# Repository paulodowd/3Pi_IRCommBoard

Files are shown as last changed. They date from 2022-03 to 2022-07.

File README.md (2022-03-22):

# 3Pi_IRCommBoard (work in progress)

<p align="center">
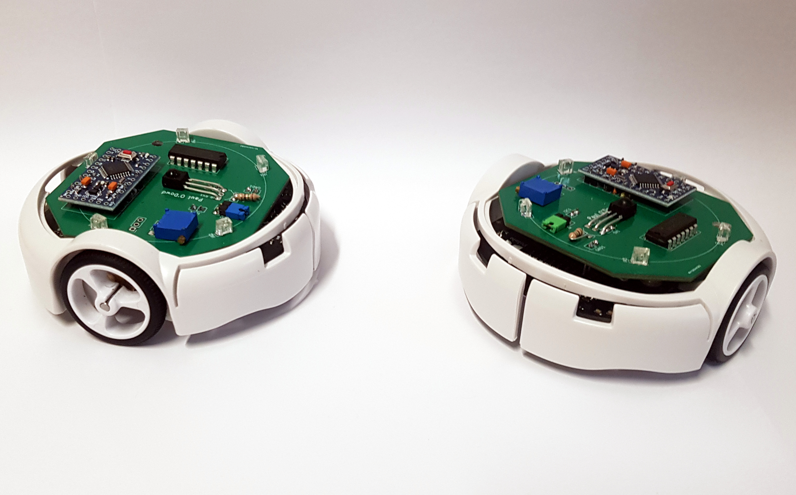
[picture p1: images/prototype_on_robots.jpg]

  </p>

## Features

- Can be considered a general purpose I2C extension board to provide local infra-red (IR) communication.
- IR Serial transmission at 4800 Baud.
- Transmit/receive upto 28 bytes (currently, extensible).
- Range can be reduced/set with a trimmer potentiometer.
- Effective IR transmit range approximately 30cm.
- Message corruption detection implemented with a CRC checksum.
- Designed to conveniently fit to an expansion header of the Pololu 3Pi+ mobile robot. 

## Summary

A pcb design to create infra-red (IR) communication between Pololu 3Pi+ robots. The design utilises an Arduino Pro Mini as an I2C Slave device.  The pro mini handles all transmit and receive operations over IR. The Master device (inteded as the 3Pi+, but could be any device with I2C) can upload a string to transmit, and also request the latest string received, if any.  This can get a little confusing to discuss: I2C is used to transfer messages between Master and Slave, and Serial/IR is used to tranmit messages between Slave devices.  

IR communication is implemented using the standard Serial functionality common to Arduino (e.g. `Serial.print()`), and so the IR circuit is electronically connected to  the Arduino TX and RX pins.  The detection (receiving) circuit uses a Demodulator chip that is tuned for a carrier frequency of 38.4Khz (more details below).  Therefore, the pro mini generates a 38Khz signal via an internal timer interrupt to provide the transmitting carrier, output on digital pin 4.  

The 38Khz carrier signal is combined electronically with the TX pin state through an OR gate (74xx32). The logic (OR) of this operation is defined by the gates sinking the current through the tranmitting IR LEDs.  Therefore, the LEDs are not driven by the 74xx32 (or the pro mini, to be clear), and are considered active low.  A nice unintended side effect of this is that when TX is inactive (LOW, not transmitting), the 74xx32 output is HIGH despite the continued 38Khz signal generation - which means the IR LEDs are off and not saturating the environment.

In this circuit design, a single gate is used to sink current.  It might be important to note that the <a href="https://www.ti.com/lit/ds/symlink/sn54hc32-sp.pdf">datasheet</a> for the logic gates specifies a max current sink of 50ma through ground - and here we are potentially sinking upto 250ma from the 5 IR LEDs.    So far, I've not seen any significant changes to performance and this may be because I am not sinking current continuously, instead intermitently at 38Khz. In a subsequent design (available <a href="https://github.com/paulodowd/Swarm-Bs">here</a>), all 4 gates are ganged, but the internal ground connection may still be a limitation. In either case, I haven't yet seen any problems or difference in performance.  It might be unwise to active the IR LEDs continuously.

Some messages transmitted over IR do get garbled.  As a quick solution, the firmware uses a CRC checksum.  I've used the same implementation as detailed on the RepRap wiki for GCode (<a href="https://reprap.org/wiki/G-code#Checking">here</a>).  Prior to transmitting, the pro mini generates a single byte checksum value, and appends this to the message string.  Therefore, when a message is received, the receiving pro mini completes the same CRC check on the received message for itself, and then compares if the checksum values match.  If not, some data must be corrupt and the message is discarded.  

The message strings transmitted between the pro mini devices would look something like:

`*message string@f`

Here, the `*` is used to identify the start of a message, the `@` is used to identify the end of the message and that the next byte is the checksum value.  In the example above, I haven't used the correct checksum value, it is just an illustrative example.  The transmission is also made with a `\n` character at the end, but this is discarded.  

At the moment, the pro mini firmware will only store 1 message, the latest message received.  Furthermore, it is programmed to erase this message after 1 second.  This suits the intended use of the board, but will likely need updating for other uses.  

When the Master device requests the latest message from the pro mini Slave device, it will receive a string terminated with a `!` character.  If the Master receives:

`!` 

This means that no messages are available.  Otherwise, the Master can parse the received bytes over I2C and use the `!` to identify the end of the string (more details below).  

If the Master is to set a string for the pro mini Slave to transmit over IR, this should be sent over I2C with no terminating character (e.g., no newline, or anything specific, just the string you wish to transmit).  Here, it is unknown (not tested!) what will happen if your string has an `*`, `\n` or `!` in it - it will probably break functionality!  Whilst this is inconsistent from the format used for messages between the pro mini Slave devices, it presents the simplest usage/interface when working with the Master device - all the tokens and CRC are handled for the user.

Software is still sketchy early work for proof-of-concept.

## Important Considerations

- **IR Demodulator:** I tried a few IR demodulator chips and they are not all created equally.  In particular, those designed to receive bursts of transmission appear poorly suited.  When using ones for burst transmission, I observed that I had to wave the transmitter or receiver around to get a successful transmission (perhaps some inner circuitry reaches a saturation?).  Instead it is better to use those designed for continuous transmission. The Vishay **TSDP34138** (<a href="https://www.farnell.com/datasheets/2245004.pdf">datasheet</a>) seems to fit this and works well / reliably.  The datasheet specifies upto 4800 baud for a 38.4Khz carrier frequency.  If you want to reproduce this board, I recommend you use the same device, or be ready for some trials of different devices.
- **IR Demodulator Placement:** The IR Demodulator (IRD) is placed central on the PCB and facing upwards - this probably isn't the manufacturers recommendation for optimal performance.  I did consider placing 5 IRD's around the circumference of the PCB facing outward between the IR LEDs.  However, the IRD is one of the more expensive components, and so producing 100 of these PCBs would be significantly more expensive with 5 IRD per board.  I have tested this PCB with 1 upward IRD and it can reliably detect IR transmission from neighbours at roughly 30cm distance.  For communication between Pololu 3Pi+ robots, this is relatively "local" and sufficient.  However, it does mean a robot cannot identify from which direction a transmission was received.  In theory, I think a more advanced version of this board could supply VCC to 5 independent IRD via the arduino digital pins, and therefore poll the IRD around the circumference of the board by enabling each in turn, and so infer directionality.  But I haven't tried this. 
- **Self-Receiving:** I did have an issue of a single board receiving it's own IR transmissions, and not being able to receive transmission from neighbours.  I believe this is because the UART implementation (on the Atmega328 at least) operates send (TX) and receive (RX) independently.  When using IR light, this means it will detect it's own transmission. After attempting a lot of different solutions, it was as simple as disabling the RX functionality of the UART by a register operation.  I'm glad this was available!  You can review the details of this on page 171 of the Atmega328 datasheet (<a href="https://ww1.microchip.com/downloads/en/DeviceDoc/Atmel-7810-Automotive-Microcontrollers-ATmega328P_Datasheet.pdf">here</a>).  You can find this operation in the firmware about <a href="https://github.com/paulodowd/3Pi_IRCommBoard/blob/922e04242b78fc39a44c0d518355c1a5028df249/arduino/pro_mini_firmware/pro_mini_firmware.ino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">here</a>.
- **Programming the Pro Mini:** It is important to note that the programming of the Pro Mini will most often fail if the IR Demodulator is electronically connected.  Therefore, the circuit design has a jumper (labelled, "RX Break") intended for a connecting removable sleeve, to allow the connection to be broken for programming.  Importantly, no IR messages can be received if this jumper is not closed with the sleeve.  
- **I2C requests from Master:** so far, it seems that the Master device has to request a specific number of bytes from the Slave device.  Because we don't necessarily know this before hand (and to take a short cut), the firmware has been written to append a `!` character to the end of the message string.  Therefore, the Master requests the maximum data length, and then parses for the `!` character.  After this, the data is gibberish.  In the future, it might be better to have a two step operation where the Master first asks how large the data to transfer is.  
- **Buffer Sizes:** The current buffers for sending and receiving IR messages in the firmware are set to 32 bytes (`MAX_MSG = 32`).  The IR transmission is operated by the Arduino Serial functionality.  By default, the Arduino environment sets the Serial buffer to 64 bytes.  Here, I decided to keep the Serial buffer under-utilised (half-full).  My un-tested rationale was to stand a chance of successfully parsing a whole 32-byte message within a 64-byte buffer.  I believe it is possible to expand the default Serial buffer beyond 64 bytes.  These aspects are open for investigation.  But for now, it is recommended to send a string of max length 28 bytes (leaving 4 bytes free for `*`, `@` and the checksum value).  The current buffer implementation for the IR messages is not very clever, e.g. not circular or anything like that.  I haven't validated the reliability of the transmission when the maximum buffer is used. 
- **Buffer Sizes:** The current buffers for sending and receiving IR messages in the firmware are set to 32 bytes (`MAX_MSG = 32`).  The IR transmission is operated by the Arduino Serial functionality.  By default, the Arduino environment sets the Serial buffer to 64 bytes.  Here, I decided to keep the Serial buffer under-utilised (half-full).  My un-tested rationale was to stand a chance of successfully parsing a whole 32-byte message within a 64-byte buffer.  I believe it is possible to expand the default Serial buffer beyond 64 bytes.  These aspects are open for investigation.  But for now, it is recommended to send a string of max length 28 bytes (leaving 3 bytes free for `*`, `@`, the checksum value and `\n`).  The current buffer implementation for the IR messages is not very clever, e.g. not circular or anything like that.  I haven't validated the reliability of the transmission when the maximum buffer is used. 
- **IR Message Buffers:** to buffer messages being sent and received, there are 3 buffers in total. 1) a buffer to hold the message to transmit as set by the Master 2) a buffer to process a received message 3) a buffer to hold the last correctly validated message to relay to the Master.  Therefore, buffer 2 could be considered volatile - hence the need for 3 buffers.  
- **IR LED current:**  In this circuit design, a single gate is used to sink current.  It might be important to note that the <a href="https://www.ti.com/lit/ds/symlink/sn54hc32-sp.pdf">datasheet</a> for the logic gates specifies a max current sink of 50ma through ground - and here we are potentially sinking upto 250ma from 5 IR LEDs.    So far, I've not seen any significant changes to performance and this may be because I am not sinking current continuously. In a subsequent design (available <a href="https://github.com/paulodowd/Swarm-Bs">here</a>), all 4 gates are ganged, but the internal ground connection may still be a limitation. In either case, I haven't yet seen any problems or difference in performance.  It might be unwise to active the IR LEDs continuously.

## Bill of Materials (BOM)

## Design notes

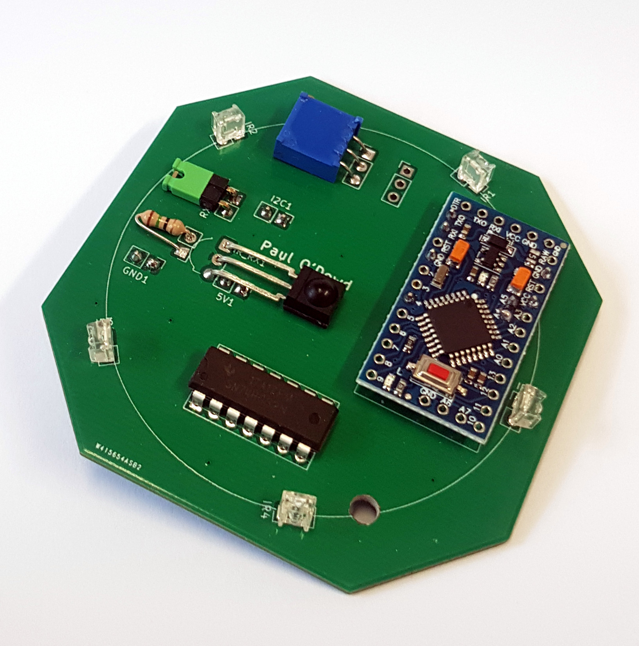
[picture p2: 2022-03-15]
images/board_prototype.jpg

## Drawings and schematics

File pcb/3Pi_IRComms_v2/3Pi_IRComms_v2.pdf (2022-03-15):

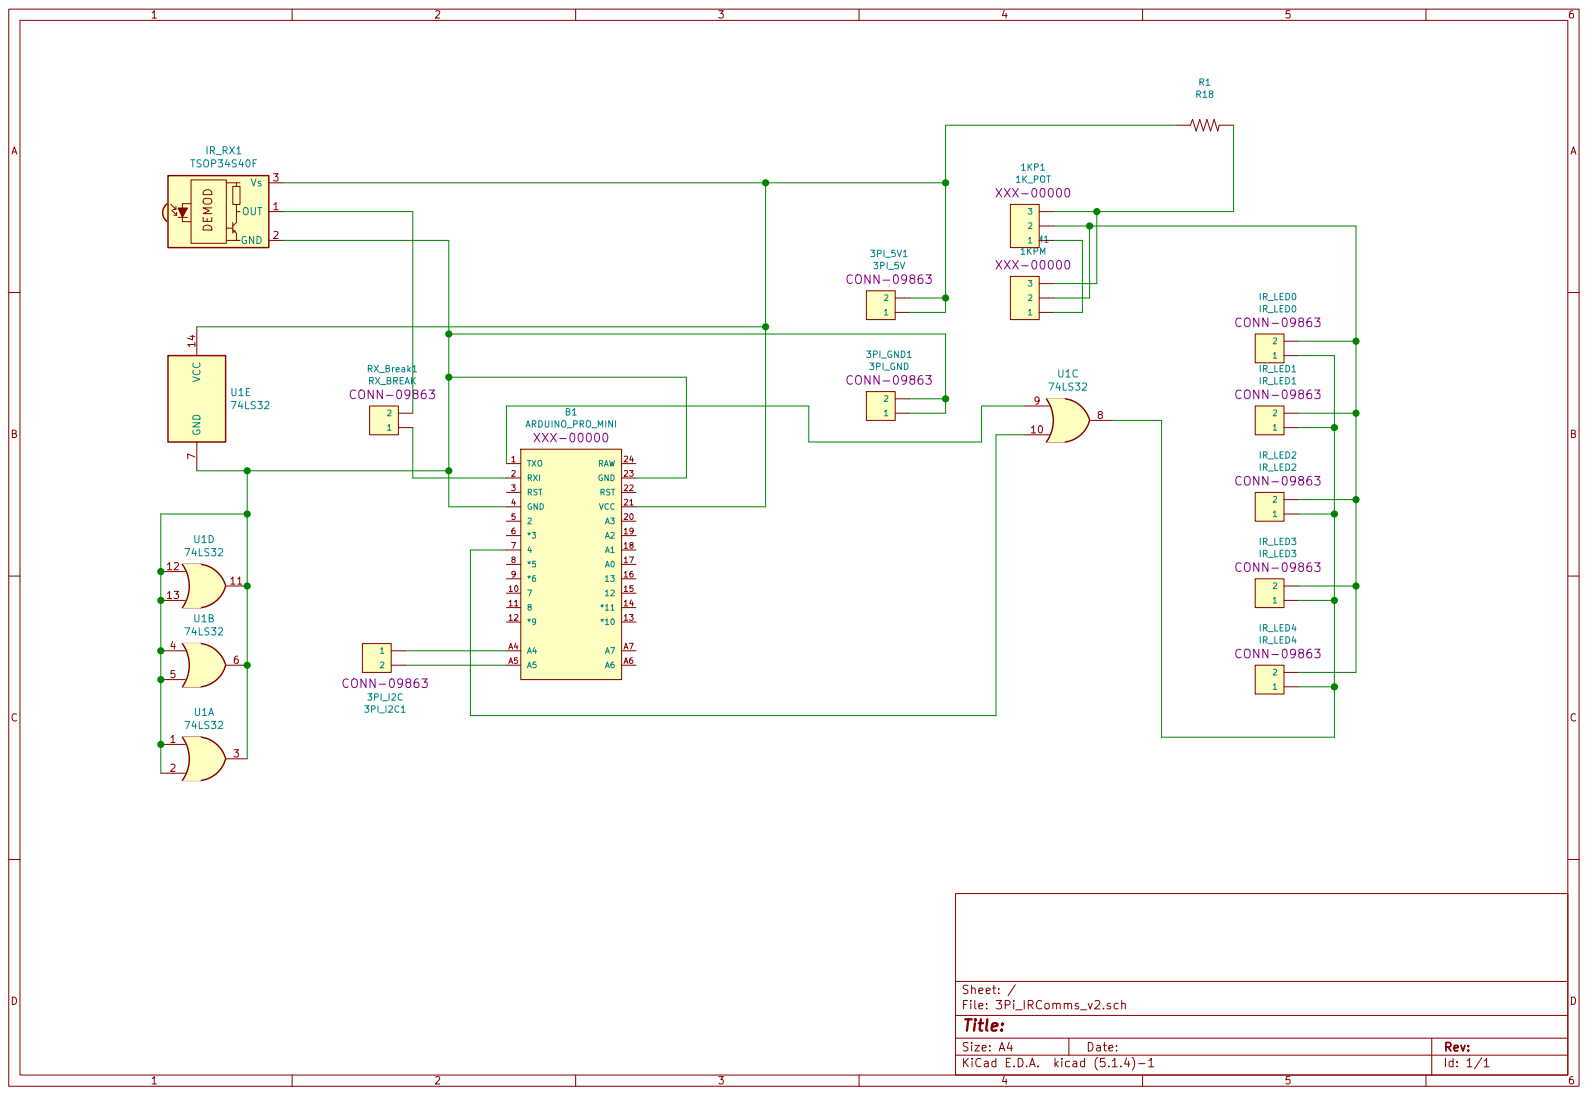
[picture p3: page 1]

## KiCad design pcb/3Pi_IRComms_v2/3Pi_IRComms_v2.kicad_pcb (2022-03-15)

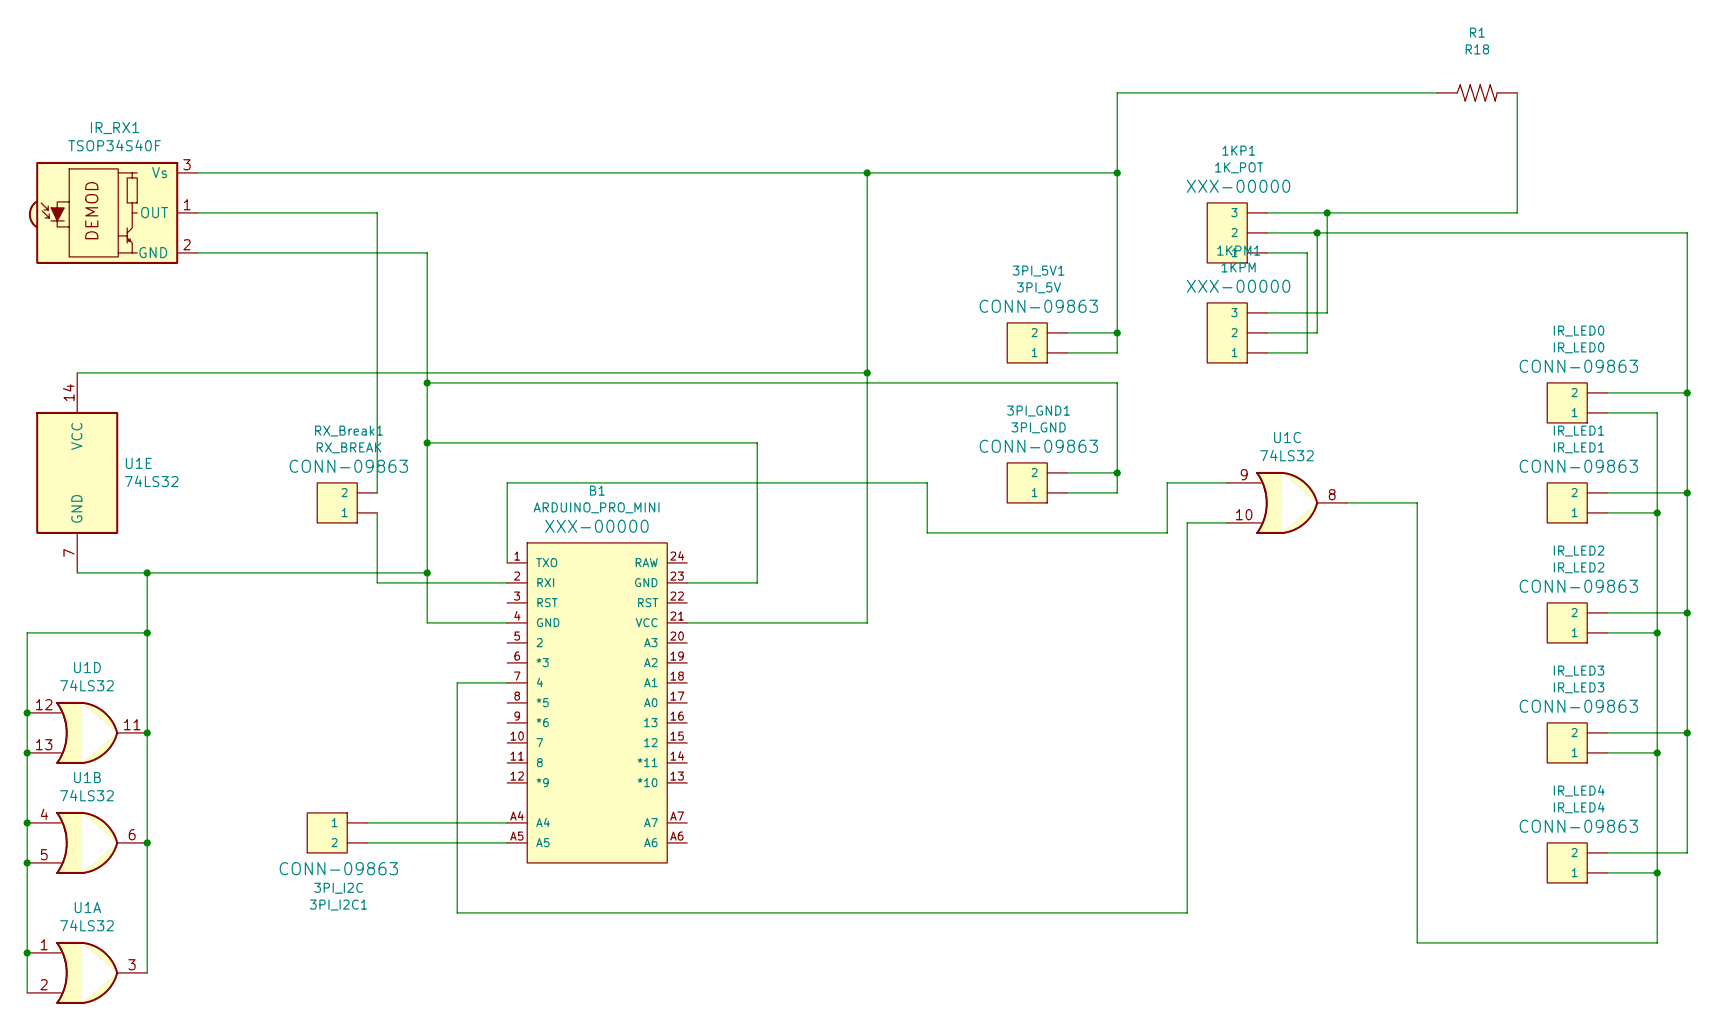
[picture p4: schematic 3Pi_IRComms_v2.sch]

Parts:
1KP1: 1K_POT; PinHeader_1x03_P2.54mm_Vertical
1KPM1: 1KPM; PinHeader_1x03_P2.54mm_Vertical
3PI_5V1: 3PI_5V; PinHeader_1x02_P2.54mm_Vertical
3PI_GND1: 3PI_GND; PinHeader_1x02_P2.54mm_Vertical
3PI_I2C1: 3PI_I2C; PinHeader_1x02_P2.54mm_Vertical
B1: ARDUINO_PRO_MINI
IR_LED0: IR_LED0; PinHeader_1x02_P2.54mm_Vertical
IR_LED1: IR_LED1; PinHeader_1x02_P2.54mm_Vertical
IR_LED2: IR_LED2; PinHeader_1x02_P2.54mm_Vertical
IR_LED3: IR_LED3; PinHeader_1x02_P2.54mm_Vertical
IR_LED4: IR_LED4; PinHeader_1x02_P2.54mm_Vertical
IR_RX1: TSOP34S40F; Vishay_MOLD-3Pin
R1: R18; PinHeader_1x02_P2.54mm_Vertical
RX_Break1: RX_BREAK; PinHeader_1x02_P2.54mm_Vertical
U1: 74LS32; DIP-14_W7.62mm_Socket

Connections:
unnamed: 1KP1.1, 1KPM1.1
unnamed: 1KP1.2, 1KPM1.2, IR_LED0.2, IR_LED1.2, IR_LED2.2, IR_LED3.2, IR_LED4.2
unnamed: 1KP1.3, 1KPM1.3, R1.2
unnamed: 3PI_5V1.1, 3PI_5V1.2, B1.21 (VCC), IR_RX1.3 (Vs), R1.1, U1.14 (VCC)
unnamed: 3PI_GND1.1, 3PI_GND1.2, B1.4 (GND), B1.23 (GND), IR_RX1.2 (GND), U1.1, U1.2, U1.3, U1.4, U1.5, U1.6, U1.7 (GND), U1.11, U1.12, U1.13
unnamed: 3PI_I2C1.1, B1.A4
unnamed: 3PI_I2C1.2, B1.A5
unnamed: B1.1 (TXO), U1.9
unnamed: B1.2 (RXI), RX_Break1.1
unnamed: B1.7 (4), U1.10
unnamed: IR_LED0.1, IR_LED1.1, IR_LED2.1, IR_LED3.1, IR_LED4.1, U1.8
unnamed: IR_RX1.1 (OUT), RX_Break1.2

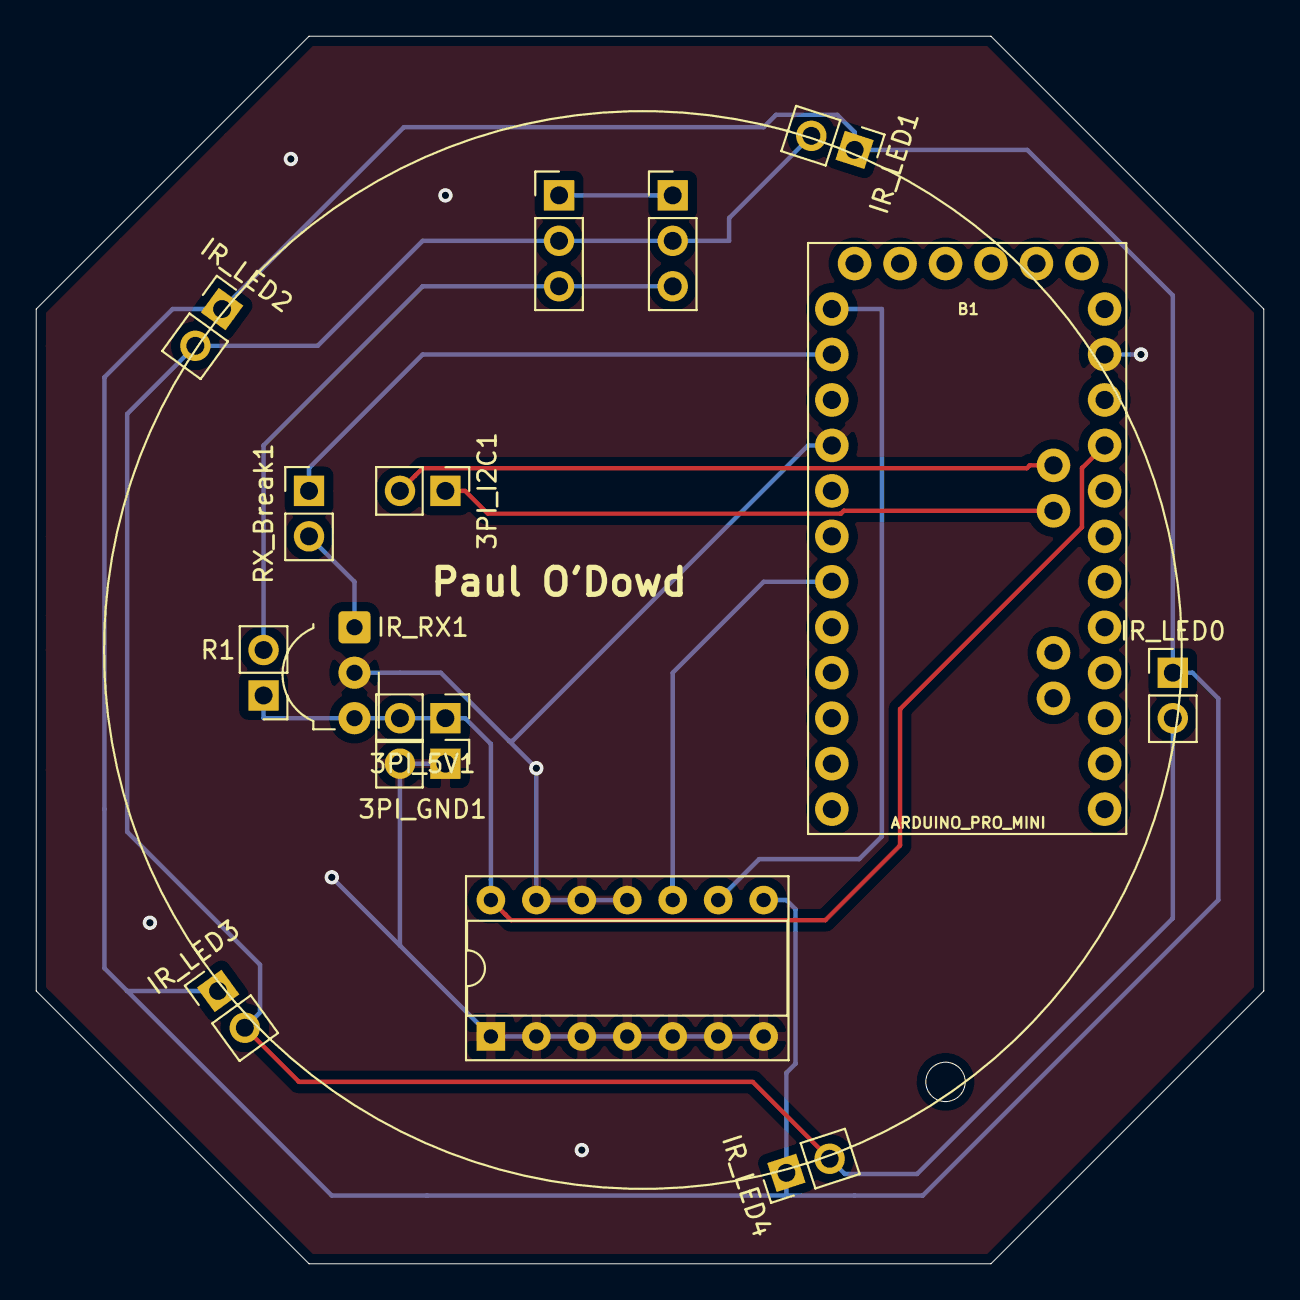
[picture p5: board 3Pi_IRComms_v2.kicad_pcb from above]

Board: 2 copper layers, 68.6 x 68.6 mm, 15 parts (0 on the bottom side), 12 nets.

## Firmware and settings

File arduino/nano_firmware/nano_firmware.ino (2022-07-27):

/*
   i2c slave device to handle IR messaging between
   3pi+ robots.
*/
#include <avr/io.h>
#include <Wire.h>
#define I2C_ADDR 8

boolean LED;      // debug LED
unsigned long ts; // general time stamp, timeout for
                  // debug LED.

#define POT_A A0
#define POT_B A1
#define POT_C A2

// Two operational states
#define STATE_IR_TX_ON 1
#define STATE_IR_TX_OFF 2
int state = STATE_IR_TX_ON;


#define MAX_MSG 32
static char tx_buf[MAX_MSG];  // buffer for IR out (serial)
static char rx_buf[MAX_MSG];  // buffer for IR in  (serial)
static char rx_msg[MAX_MSG];  // holding buffer for msg down 
                              // to Master over i2c
int rx_count;

// 38Khz signal generated on
// digital pin 4.
#define TX_CLK_OUT 4

unsigned long msg_ttl; // msg time to live
#define TTL 1000       // keep a message for 1 second
                       // then delete. 

unsigned long tx_ts;    // transmit time-stamp
unsigned long tx_delay; // delay between tx
unsigned long tx_delay_min;
unsigned long tx_delay_extra;

// Flags
boolean BROADCAST = false;
boolean PROCESS_MSG = false;
#define LED_B 9
#define LED_G 10
#define LED_R 11

#define DEBUG_LED 13

void setup() {

  // Set random seed.
  initRandomSeed();

  // Set pin for 38khz carrier as output
  pinMode(TX_CLK_OUT, OUTPUT);

  // Debug led
  pinMode(13, OUTPUT);
  
  // RGB LED
  pinMode( LED_R, OUTPUT );
  pinMode( LED_G, OUTPUT );
  pinMode( LED_B, OUTPUT );

  // Debugging LED
  pinMode(DEBUG_LED, OUTPUT );
  digitalWrite(DEBUG_LED, LOW);

  // Input pots
  pinMode( POT_A, INPUT );
  pinMode( POT_B, INPUT );
  pinMode( POT_C, INPUT );
  
  // Set message buffers to invalid (empty) state
  memset( tx_buf, 0, sizeof( tx_buf ));
  memset( rx_buf, 0, sizeof( rx_buf ));
  memset( rx_msg, 0, sizeof( rx_msg ));

  // Set initial tx_delay variables
  tx_delay_min = 500;
  tx_delay_extra = 500;
  

  // Setup Timer 2 to help generate a 38khz signal.
  setupTimer2();

  // Begin I2C, note, as a slave device.
  Wire.begin( I2C_ADDR );
  Wire.onRequest( reportLastMessage );
  Wire.onReceive( newMessageToSend );

  // Start Serial.  Note, here we are using
  // serial to transmit strings over IR by
  // modulating it with the 38khz carrier.
  // The IR demodulator chip can support
  // baud up to 4800, but other variants 
  // might not.
  Serial.begin(4800);
  Serial.setTimeout(500);

  // Set initial time-stamp values
  ts = millis();
  msg_ttl = millis();

  tx_ts = millis();
  setTXDelay();
  //disableTX();
  resetRxBuf();
}


// Experiment to see if reading the LSB
// of an analog read can generate a 
// useful random seed.  Nothing connected
// to A0.  I think the LSB fluctuates 
// randomly(?)
void initRandomSeed() {
  pinMode(A0, INPUT);
  byte r = 0x00;
  for ( int i = 0; i < 8; i++ ) {
    byte b = (byte)analogRead(A0);
    b = b & 0x01;
    r |= (b << i);
    delayMicroseconds(2);
  }
  randomSeed( r );
}

// Attempting an asynchronous send
// and listen procedure because we
// can't do both at the same time.
// https://lucidar.me/en/serialib/most-used-baud-rates-table/
// We are using 4800 baud, which is 
// 4800 bits per second.
// 1.042ms per byte.
// So we space transmission by 35ms
// to allow for receipt, and pad/vary
// by upto 50ms(?)
void setTXDelay() {
  float t = (float)random(0, tx_delay_extra); // 0:50
  t += tx_delay_min; // 35
  // Insert random delay to help
  // break up synchronous tranmission
  // between robots.
  tx_delay = (unsigned long)t;
}

void setRGB( int r, int g, int b ) {
  if( r == 0 ) {
    digitalWrite( LED_R, LOW );
  } else {
    digitalWrite( LED_R, HIGH );
  }

  if( g == 0 ) {
    analogWrite( LED_G, 0 );
  } else {
    analogWrite( LED_G, 128 );
  }


  if( b == 0 ) {
    analogWrite( LED_B, 0 );
  } else {
    analogWrite( LED_B, 128 );
  }
  
}

// This ISR simply toggles the state of
// pin D4 to generate a 38khz clock signal.
ISR( TIMER2_COMPA_vect ) {
  PORTD ^= (1 << PD4);

}

// We use Timer2 to generate a 38khz clock
// which is electronically OR'd with the
// serial TX.
void setupTimer2() {

  // Termporarily stop interupts
  cli();
  
  // Setup Timer 2 to fire ISR every 38khz
  // Enable CTC mode
  TCCR2A = 0;
  TCCR2A |= (1 << WGM21);

  // Setup ctc prescaler
  TCCR2B = 0;

  // No prescale?
  //TCCR2B |= (1<<CS21);
  TCCR2B |= (1 << CS20);

  // match value
  OCR2A = 210; // counts to 53, every 38,000hz
  //OCR2A = 53; // counts to 53, every 38,000hz


  // Set up which interupt flag is triggered
  TIMSK2 = 0;
  TIMSK2 |= (1 << OCIE2A);

  // enable interrupts
  sei();

}


byte CRC( String in_string ) {
  String buf;
  byte cs;
  int i;

  cs = 0;
  for ( i = 0;  i < (int)in_string.length(); i++ ) {
    cs = cs ^ in_string.charAt(i);
  }
  cs &= 0xff;

  return cs;
}

// Over i2c to Master
// Sends a string of the latest message received from
// other robots.
// If the buffer is empty, a ! character is sent. 
// Note, a correct message should also end in !
void reportLastMessage() {

  // No message.
  if ( rx_msg[0] == 0 ) {
    Wire.write("!");
  } else {
    Wire.write( rx_msg, strlen(rx_msg) );
  }

}

// For IR.
// Function to format a message for our
// IR transmission.  We use:
// * to indicate the start of a message
// @ to indicate a checksum value following
void newMessageToSend( int len ) {
  //Serial.println(len);
  //digitalWrite(13, HIGH);
  int count = 0;

  // Stop transmission whilst we update
  // the buffer.
  state = STATE_IR_TX_OFF;

  // Clear tx buffer
  memset( tx_buf, 0, sizeof( tx_buf ) );

  // set first character as our message
  // start byte
  tx_buf[count++] = '*';

  // Should we add a timeout here?
  // Receive up until buffer -1
  while ( Wire.available()  ) {
    char c = Wire.read();
    tx_buf[count] = c;
    count++;
  }

  // We could add in here a special character 
  // to erase tx_buf and set the board to stop
  // transmitting.
  // Have more than just * in the buffer
  /*
  if( count > 1 ) {

    // Special first characters
    if( tx_buf[1] == '!' ) {          // Clear transmit message
      memset( tx_buf, 0, sizeof( tx_buf ) );
      return;
      
    } else if( tx_buf[1] == '£' ) {   // Set tx_delay period?
      

    } else if( tx_buf[1] == '#' ) {   // Set RGB?

    }
  }
  */

  // Add crc
  byte cs;
  int i;

  cs = 0;
  for ( i = 0;  i < count; i++ ) {
    cs = cs ^ tx_buf[i];
  }
  cs &= 0xff;

  tx_buf[count++] = '@';
  tx_buf[count++] = cs;


  //Serial.println( count );
  //Serial.println( tx_buf );

  // Restart IR transmission
  state = STATE_IR_TX_ON;
}


// The arduino pro mini has a parallel serial
// interface,meaning with IR it can receive
// it's own tranmission. There, we access the 
// UART register to disable RX functionality.
// When we re-enable it, this has the beneficial
// side-effect of clearing the input buffer.

void disableRX() {
  cli();
  UCSR0B &= ~( 1 << RXEN0 );
  UCSR0B &= ~( 1 << RXCIE0 );
  sei();
}

// Re-enable the serial port RX hardware.
void enableRX() {

  
  cli();
  UCSR0A &= ~(1 << FE0);
  UCSR0A &= ~(1 << DOR0);
  UCSR0A &= ~(1 << UPE0);
  UCSR0B |= ( 1 << RXEN0 );
  UCSR0B |= ( 1 << RXCIE0 );
  sei();
}

// Clears our received buffer
void resetRxBuf() {
  rx_count = 0;
  PROCESS_MSG = false;
  memset( rx_buf, 0, sizeof( rx_buf ) );
}



void loop() {

 

  // Toggle whether we are broadcasting
  // or listening for IR messages
  if ( millis() - tx_ts > tx_delay ) {
    BROADCAST = !BROADCAST;
    tx_ts = millis();

    // Set a different delay for next
    // iteration
    setTXDelay();
  }


  // If we are in broadcast mode and the LEDS
  // are active.
  if ( state == STATE_IR_TX_ON && BROADCAST) {

    // If we have not received a message from
    // the Master over i2c, do nothing.
    if ( tx_buf[0] == 0 ) {
      // don't send, empty buffer.
      
    } else { // Message from Master to send.

      // We have a problem where we pick up
      // our own reflected transmission.
      disableRX();
      //enableTX();

      // Using Serial.print transmits over
      // IR.  Serial TX is modulated with
      // the 38Khz carrier in hardware. 
      digitalWrite(DEBUG_LED, HIGH);
      Serial.println( tx_buf );
      Serial.flush(); // wait for send to complete
      digitalWrite(DEBUG_LED, LOW);
      
      //disableTX();

      // With TX finished, we can receive again
      // and not get our own transmission.
      enableRX();

    }
  }


  // Clear old messages received via IR.
  if ( millis() - msg_ttl  > TTL ) {
    memset( rx_msg, 0, sizeof( rx_msg ) );
    msg_ttl = millis();
  }

  // Clear status LED
  if ( millis() - ts > 100 ) {
    ts = millis();
    digitalWrite( 13, LOW );
    setRGB( 1, 0, 0 );
    //analogWrite(LED_R, 255 );
    //analogWrite(LED_G, 0);
    // Debug
    //Serial.print("last message: ");
    //Serial.print( rx_msg );
    //Serial.print(" ");
    //Serial.println( ts );
  }


  // See if we have received over IR to
  // process. 
  while ( Serial.available() && !PROCESS_MSG ) {

    // If we find a newline, we flag we have
    // a message to attempt to process.
    rx_buf[rx_count] = Serial.read();
    if ( rx_buf[ rx_count ] == '\n' ) PROCESS_MSG = true;


    // Note that, it might seem like rx_count will
    // exceed the buffer. The next check should 
    // catch this, and cause the buffer to be 
    // processed.  We don't zero rx_count on each
    // call of loop() because we may only have a
    // few characters in the Serial buffer.  So we
    // need to incrementally fill our rx_buf with
    // many calls to this while loop.
    // Processing the message will reset rx_count
    // to 0.
    rx_count++;

    // If we exceed the buffer size, we also
    // will try to process the message.
    if ( rx_count >= MAX_MSG ) PROCESS_MSG = true;
  }

  // Do we think we have a message to process?
  if ( PROCESS_MSG ) {

    // Debug
    //Serial.print("got "); Serial.print(rx_buf); Serial.print(":"); Serial.println(rx_count);

    // Invalid conditions:
    if ( rx_count <= 0 || rx_buf[0] == 0 ) {
      // bad read.
      //Serial.println("bad serial");

     
    } else {  // Valid rx buf

      // Check for start byte
      int start = -1;  // -1 = default error state

      // Search string for * symbol (start)
      // Save index
      for ( int i = 0; i < rx_count; i++ ) {
        if ( rx_buf[i] == '*') {
          start = i;
          break;
        }
      }

      // Message too short or bad
      // e.g. a useless message would be:
      //      *abcdef@a  (start,message,CRC token, CRC value)
      //      minimum (absurd) message would be *@_
      //      min message length = 3
      // if start < 0, then no * symbol was found
      if ( (rx_count - start) <= 3 || start < 0 ) {
        //Serial.println("message too short :(");

      } else { // message valid, * index found

        // Check CRC, find @ token to separate
        // out CRC value.
        int last = -1;
        for ( int i = 0; i < rx_count; i++ ) {
          if ( rx_buf[i] == '@') {
            last = i;
            break;
          }
        }

        // Start should be 0 or more
        // Note, we include the start byte *
        // in the checksum
        if ( last > start && last < (rx_count - 1) ) {
          char buf[rx_count];
          int b = 0;  // count how many bytes
          
          // we copy.
          for ( int i = start; i < last; i++ ) {
            buf[b] = rx_buf[i];
            b++;
          }

          // We need at least 1 byte of data
          // between start and checksum
          if ( b >= 1 ) {
            //Serial.print("copied: " );
            //Serial.print( buf );
            //Serial.print( " b = ");
            //Serial.println(b);

            // Reconstruct checksum
            byte cs;
            cs = 0;
            for ( int i = 0;  i < b; i++ ) {
              cs = cs ^ buf[i];
            }
            cs &= 0xff;

            if ( cs == rx_buf[last + 1] ) {

              // Debug
              //Serial.println("CRC GOOD!");

              // Flash so we can see when robots are
              // receiving messages correctly
              digitalWrite(13, HIGH );
              //analogWrite(LED_R, 0 );
              //analogWrite(LED_G, 255);
              setRGB( 0, 1, 0 );

              // Make sure where we will store this
              // received message is clear.
              memset( rx_msg, 0, sizeof( rx_msg ));
              
              // Copy message across, ignoring the *
              for ( int i = 0; i < b - 1; i++ ) {
                rx_msg[i] = buf[i + 1];
              }

              // Add a ! to the message, which will be
              // used when later sending down I2C to 
              // the Master to indicate the end of the
              // string.
              rx_msg[b-1] = '!';

              // Reset TTL timestamp, so this message
              // will only exist temporarily.
              msg_ttl = millis();

            } else {
              //Serial.println("CRC BAD!");
            }
          } else {
            //Serial.println("Message payload < 1 ");
          }

        }
      }
    }

    // reset receive 
    resetRxBuf();

  }
} // end of loop

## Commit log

2022-03-16 fixed buffer error rx_count in firmware
    [pro_mini_firmware.ino]
2022-03-16 updated gerber files
    [3Pi_IRComms_v1-B_Cu.gbl, 3Pi_IRComms_v1-B_Mask.gbs, 3Pi_IRComms_v1-B_SilkS.gbo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]
